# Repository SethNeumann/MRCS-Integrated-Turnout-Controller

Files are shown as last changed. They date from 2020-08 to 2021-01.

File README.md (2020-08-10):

# REPO NAME: Integrated turnout Controller
## License: Creative Commons Attribution-NonCommercial-ShareAlike

The Integrated Turnout Controller (ITC) is designed to provide all control functions needed for remote, local, and locking of a turnout for various styles of turnout motors. The ITC provides LED outputs with onboard current limiting resistors for route and switch lock status.

The ITC can operate as a standalone turnout controller, with no computer needed. When connected to a computer for remote turnout control and the computer is not running, the ITC comes up in local mode. This allows for turnouts to be thrown manually using the Local input.

The (ITC) is an updated design of the MRCS Remote Stall Motor Controller (RSMC) introduced in 2013.

The ITC has the following features:

   - Standalone or computer turnout motor control
   - Local Throw input
   - Remote Throw input
   - Switch Lock input
   - Turnout position feedback output
   - Route LED ports, Normal/Reverse (Common Anode, Sinking)
   - Open Source sketch software
   - Motor power input, 9-12 Vdc
   - Onboard 5v regulator for logic power
   - Turnout motor driver (TC4428 MOSFET), up to 500 ma drive
   - Frog power routing using external switch contacts (Tortoise, Switchmaster™, MP1/MP5)
   - 8 position motor pads for a .156" Molex connector, .156" edge connector, or .100" (2.54mm)
   - Separate motor pads for connection to additional crossover turnout motors

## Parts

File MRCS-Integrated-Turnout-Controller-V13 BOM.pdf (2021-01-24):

ITC V 1.3 BOM

Description | Ref | Qty | Cost | Ext | Supplier | Part No.
ITC PCB | PCB1 | 1 | 0.25 | 0.25 | MRCS | ITC
AtTiny85 | U1 | 1 | 1.03 | 1.03 | Digikey | ATTINY85-20PU-ND
TC4428A MOSFET | U2 | 1 | 1.03 | 1.03 | Digikey | TC4428AEPA-ND
78L05 | U3 | 1 | 0.15 | 0.15 | Digikey | AS78L05ZTR-E1DICT-ND
Capacitor .01uF | C1,C4 | 2 | 0.14 | 0.28 | Jameco | 25507
Capacitor .33uF 35v Tantalum | C2 | 1 | 0.32 | 0.32 | Digikey | 478-1883-ND
Capacitor .1uF 35v Tantalum | C3 | 1 | 0.25 | 0.25 | Jameco | 33486
DIP Resistor Pack 1K | RP1 | 1 | 0.95 | 0.95 | Digikey | 4114R-1-102LF
Diode Shottky 1N5819 | D1 | 1 | 0.12 | 0.12 | Jameco | 177965
DIP Socket 8 pin | Tiny85,TC4428 | 2 | 0.10 | 0.20 | Jameco | 112206
8 pos Screw Terminal .100" | S1a | 1 | 0.80 | 0.80 | Amazon | GS019-2.54
4 pos Screw Terminal .100" | S1b | 1 | 0.40 | 0.40 | Amazon | GS019-2.54
8 Pin .156" RA Female Header | J1 MOLEX | 0 | 1.50 | 0.00 | Digikey | WM13505-ND
8 Pos Card Edge Connector | J1 EdgeConn | 0 | 3.50 | 0.00 | Digikey | JMT/TCONN | Sullins, connector needs shims
8 pos Screw Terminal .100" | J2 Pads | 1 | 0.80 | 0.80 | Amazon | GS019-2.54
2 Pos Screw term 0.100 | X-Over | 0 | 0.29 | - | Amazon
3 pos Screw Terminal 3.5mm | J3 FROG | 1 | 0.39 | 0.39 | Jameco | 2094514
2 pos male pin .100" | J4 THRW | 0 | 0.02 | 0.00 | Banggood | GS019-2.54
2 pos male pin .100" | J5 GND | 0 | 0.02 | 0.00 | Banggood | GS019-2.54
3 pos male pin .100" | J6 Contacts | 0 | 0.03 | 0.00 | Banggood | GS019-2.54
Page 1 of 1 | www.modelrailroadcontrolsystems.com | 1/8/2021

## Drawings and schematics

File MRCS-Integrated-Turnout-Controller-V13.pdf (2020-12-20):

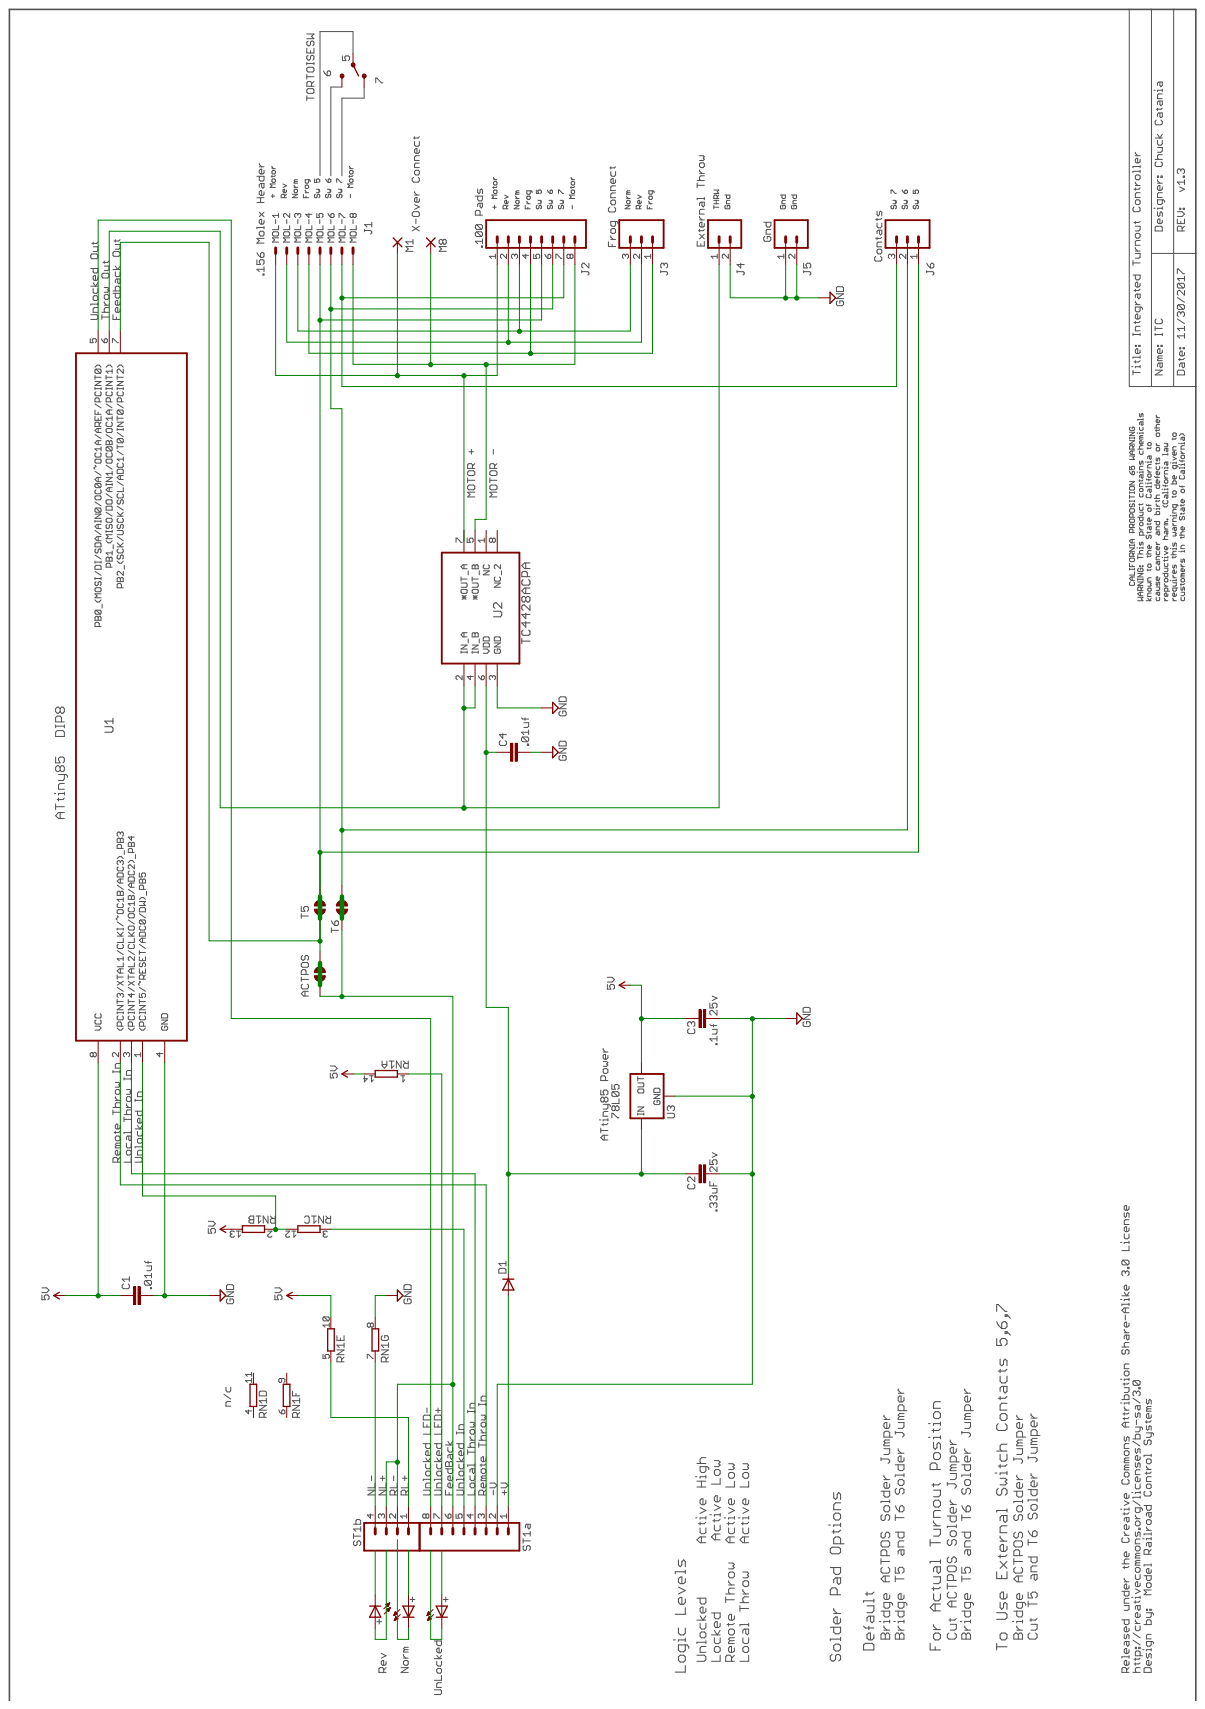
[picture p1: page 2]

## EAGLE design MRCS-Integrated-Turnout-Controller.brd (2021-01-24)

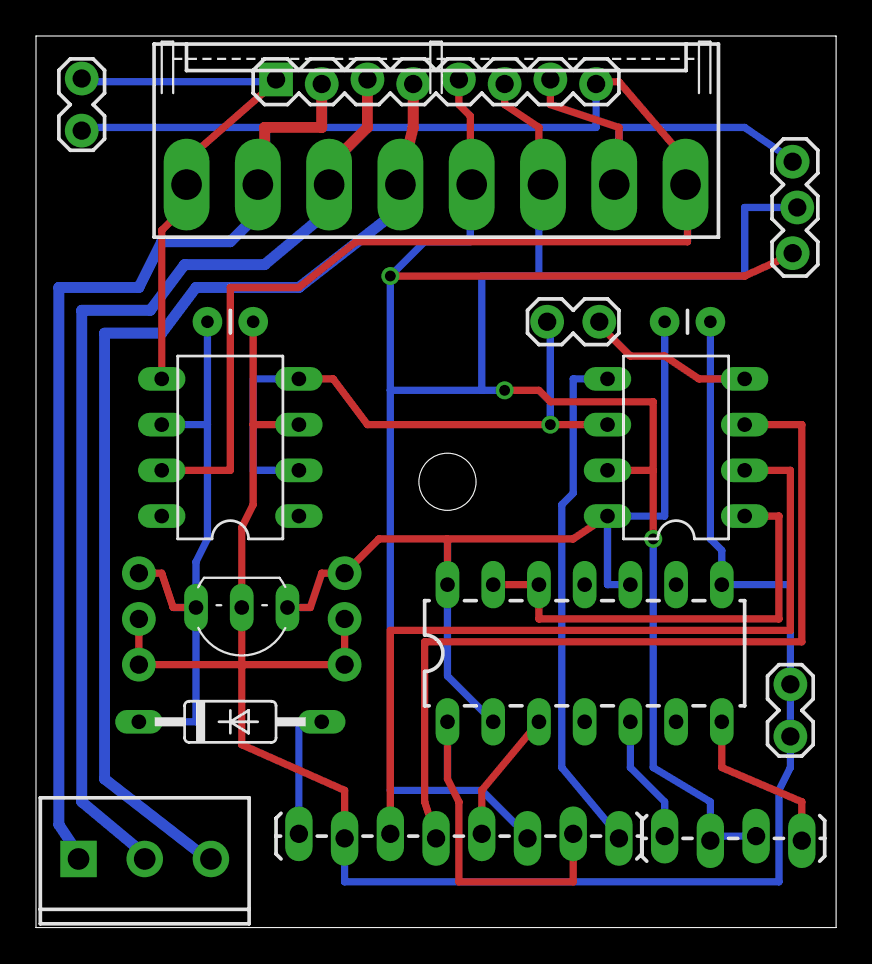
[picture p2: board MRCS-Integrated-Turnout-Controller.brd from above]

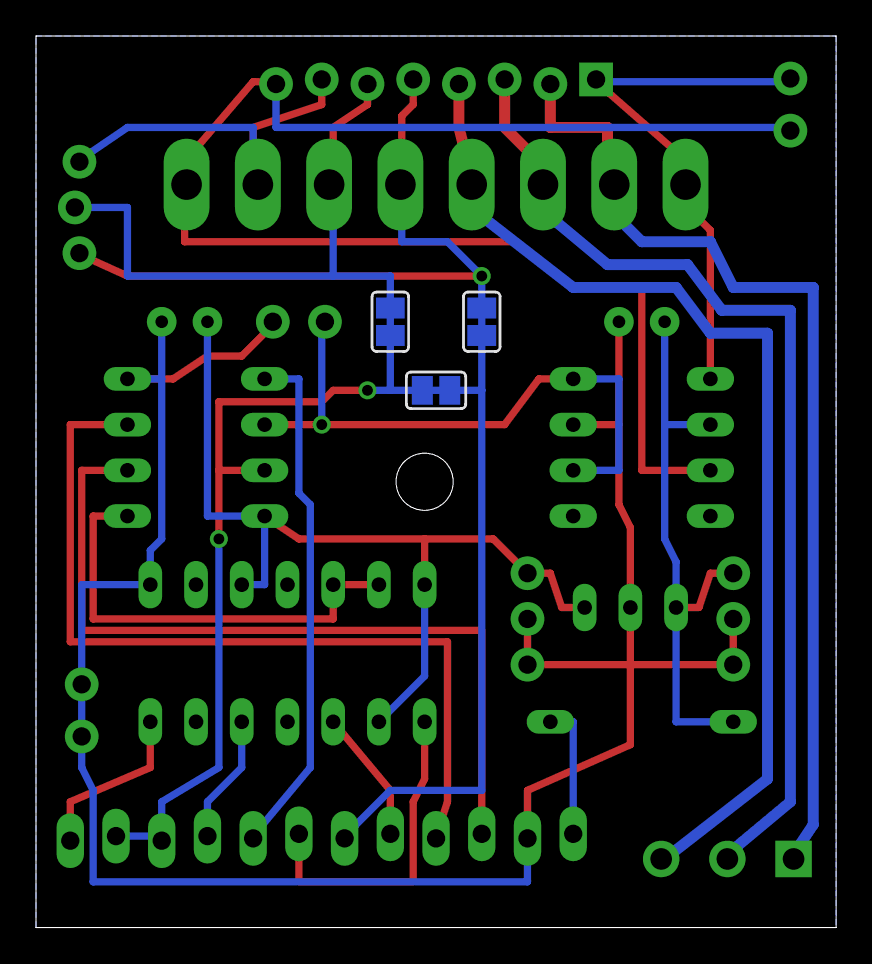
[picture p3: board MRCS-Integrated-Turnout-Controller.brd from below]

Board: 2 copper layers, 44.5 x 49.5 mm, 24 parts (3 on the bottom side), 3 nets.

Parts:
ACTPOS: SJ
C4: .01uf; CAP-PTH-SMALL
E$1: 1X08_LOCK
E$2: DRILL_0.1250
E$3: CAP-PTH-SMALL
E$4: C2992
E$5: CA-PROP65WARNING
E$6, E$18: 1X03_NO_SILK
E$7: MRCSLOGOTOP
E$8, E$11, E$13: 1X02_LOCK
E$9: 1X08_LOCK_LONGPADS
E$10: 1X04_LOCK_LONGPADS
E$12: 1X03_LOCK
FROG: SCREWTERMINAL-3.5MM-3_LOCK.007S
J1: KK-156-8-F
RN1: 1K; DIL14
T5, T6: SJ
U1: TC4428A; DIL08
U2: Tiny85; DIL08
U3: U3; TO92-BCE

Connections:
S$3: U1.4, U2.6
S$7: E$3.2, U1.3
S$29: C4.2, RN1.10, U2.8, U3.B

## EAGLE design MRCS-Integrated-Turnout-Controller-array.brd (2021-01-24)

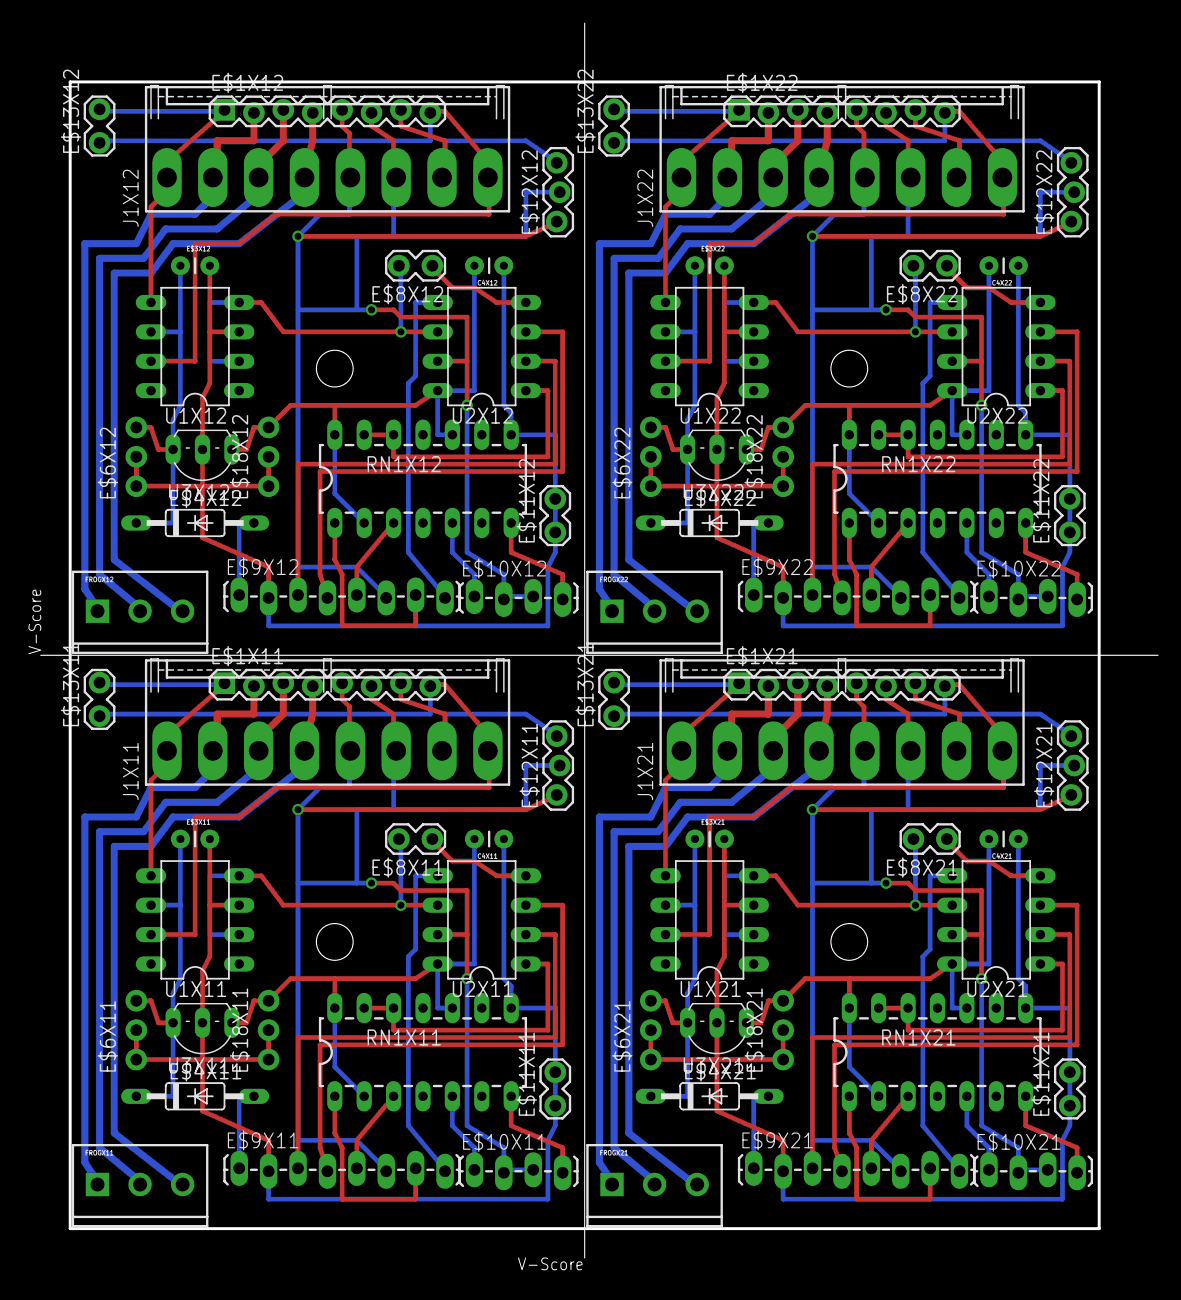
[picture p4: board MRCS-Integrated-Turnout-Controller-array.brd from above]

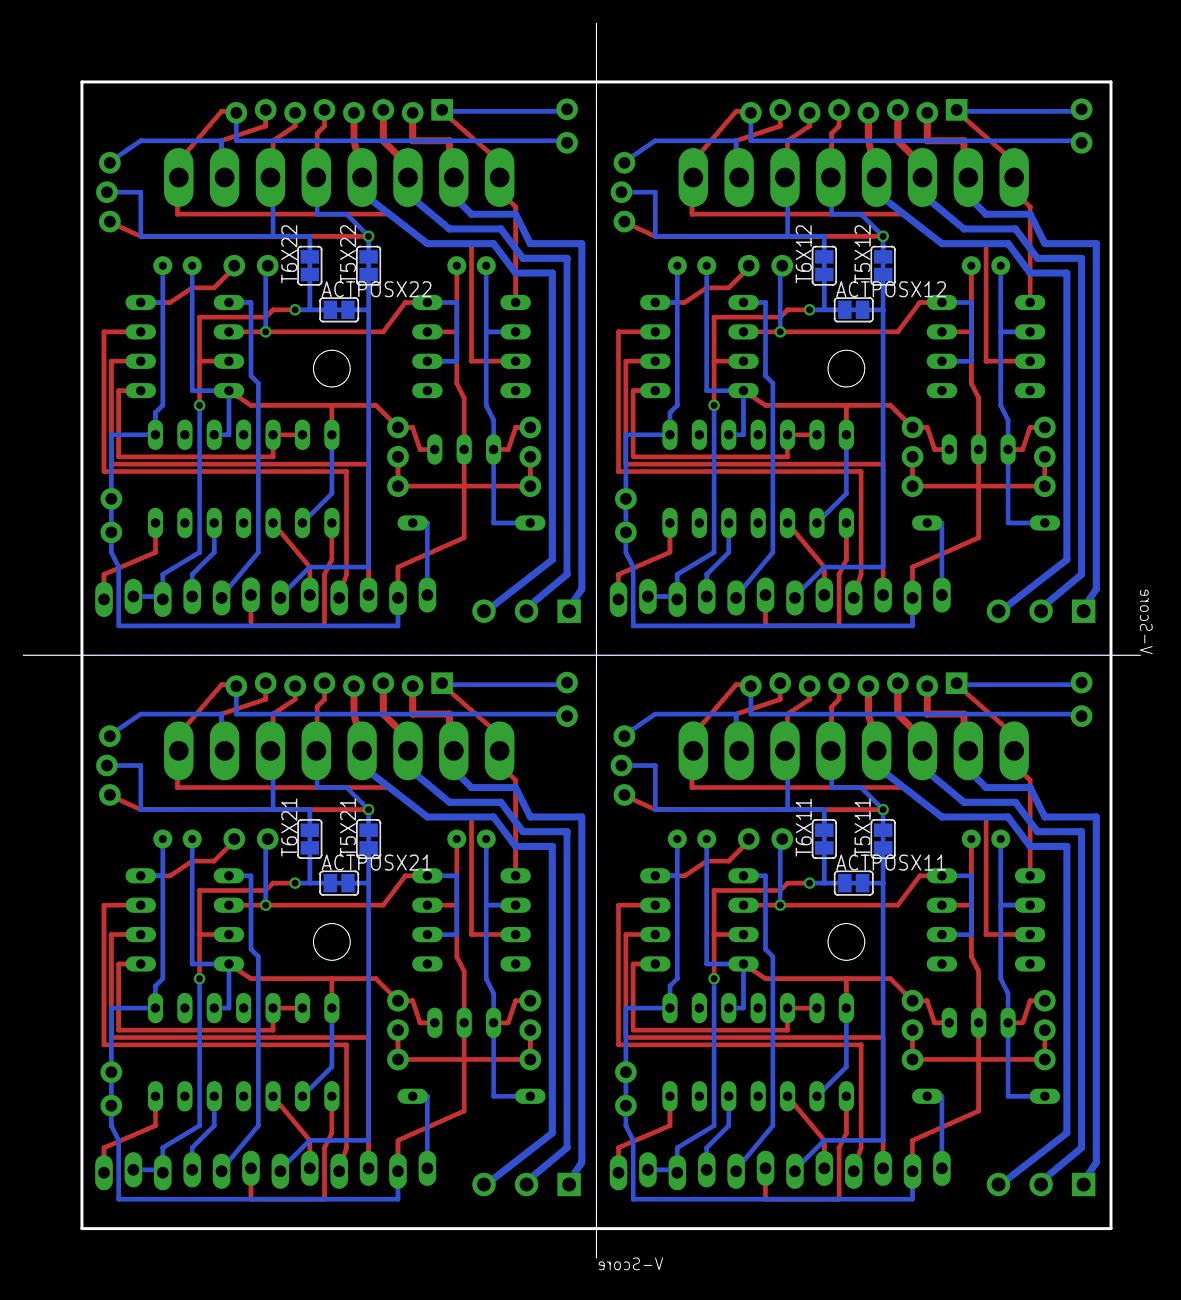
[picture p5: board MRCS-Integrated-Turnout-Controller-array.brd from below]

Board: 2 copper layers, 96.5 x 106.7 mm, 96 parts (12 on the bottom side), 12 nets.

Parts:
ACTPOSX11, ACTPOSX12, ACTPOSX21, ACTPOSX22: SJ
C4X11, C4X12, C4X21, C4X22: .01uf; CAP-PTH-SMALL
E$1X11, E$1X12, E$1X21, E$1X22: 1X08_LOCK
E$2X11, E$2X12, E$2X21, E$2X22: DRILL_0.1250
E$3X11, E$3X12, E$3X21, E$3X22: CAP-PTH-SMALL
E$4X11, E$4X12, E$4X21, E$4X22: C2992
E$5X11, E$5X12, E$5X21, E$5X22: CA-PROP65WARNING
E$6X11, E$6X12, E$6X21, E$6X22, E$18X11, E$18X12, E$18X21, E$18X22: 1X03_NO_SILK
E$7X11, E$7X12, E$7X21, E$7X22: MRCSLOGOTOP
E$8X11, E$8X12, E$8X21, E$8X22, E$11X11, E$11X12, E$11X21, E$11X22, E$13X11, E$13X12, E$13X21, E$13X22: 1X02_LOCK
E$9X11, E$9X12, E$9X21, E$9X22: 1X08_LOCK_LONGPADS
E$10X11, E$10X12, E$10X21, E$10X22: 1X04_LOCK_LONGPADS
E$12X11, E$12X12, E$12X21, E$12X22: 1X03_LOCK
FROGX11, FROGX12, FROGX21, FROGX22: SCREWTERMINAL-3.5MM-3_LOCK.007S
J1X11, J1X12, J1X21, J1X22: KK-156-8-F
RN1X11, RN1X12, RN1X21, RN1X22: 1K; DIL14
T5X11, T5X12, T5X21, T5X22, T6X11, T6X12, T6X21, T6X22: SJ
U1X11, U1X12, U1X21, U1X22: TC4428A; DIL08
U2X11, U2X12, U2X21, U2X22: Tiny85; DIL08
U3X11, U3X12, U3X21, U3X22: U3; TO92-BCE

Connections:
S$3X11: U1X11.4, U2X11.6
S$3X12: U1X12.4, U2X12.6
S$3X21: U1X21.4, U2X21.6
S$3X22: U1X22.4, U2X22.6
S$7X11: E$3X11.2, U1X11.3
S$7X12: E$3X12.2, U1X12.3
S$7X21: E$3X21.2, U1X21.3
S$7X22: E$3X22.2, U1X22.3
S$29X11: C4X11.2, RN1X11.10, U2X11.8, U3X11.B
S$29X12: C4X12.2, RN1X12.10, U2X12.8, U3X12.B
S$29X21: C4X21.2, RN1X21.10, U2X21.8, U3X21.B
S$29X22: C4X22.2, RN1X22.10, U2X22.8, U3X22.B

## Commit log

2020-08-10 clean up documentation
    change Intelligent to Integrated
    [MRCS-Integrated-Turnout-Controller.brd, MRCS-Integrated-Turnout-Controller.sch]
2021-01-24 Changes to correct U1/U2 reversal on board labels
    silk changes
    [MRCS-Integrated-Turnout-Controller-array.brd, MRCS-Integrated-Turnout-Controller.brd]

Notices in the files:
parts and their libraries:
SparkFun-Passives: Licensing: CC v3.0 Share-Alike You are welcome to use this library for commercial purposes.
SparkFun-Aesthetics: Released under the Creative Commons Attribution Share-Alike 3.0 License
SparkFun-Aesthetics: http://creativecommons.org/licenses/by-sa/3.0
